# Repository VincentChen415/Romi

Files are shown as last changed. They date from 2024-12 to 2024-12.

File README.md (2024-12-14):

# Romi



Romi is a line following differential drive robot that utilizes a NUCLEO-L476RG microcontroller with addition to encoders, IMU, IR and bump sensors. The objective of the robot is to finish a black line course with a variety of patterns/obstacles similar to the one shown above.
# Romi Demo Video:
Romi Robot Demo (https://www.youtube.com/watch?v=bHqvOkEkews)

# Mechanical Design:
## Romi Chassis


The Romi chassis includes two wheels with independent drive, an encoder for each motor, and battery slot for 6 AA batteries. For our build be also opted for rechargeable lithium-ion batteries in order to limit the total cost throughout the prototyping and development process. The Romi chassis also has two rollers to prevent tipping of the robot. In addition to these aspects, the chassis also has numerous mounting points of various sizes to account for a wide range of compatible components.
## 3D-Printed Brackets


# Romi Electrical Design:
## Nucleo L476 w/ Shoe of Brian



For this Project we used a Nucleo L476 development board. This board was chosen due to the affordable and flexible nature of it. This board was also based of the STM32L476RG, which is a 32-bit ARM Cortex-M4 microcontroller with a FPU and offers very powerful processing capabilities. This board also offers a wide range of peripherals, making this a great choice for this project. This board was also paired with Shoe of Brain to provide additional outputs and additional capabilities.
## Motor Driver and Power Distribution Board for Romi Chassis


The main purpose of the motor driver and power distribution board is to step down the voltage to 5V and supply a continuous 2.5A current. The board features two DRV8838 motor drivers. The phase pin controls direction and the enable pin is a PWM input that can control the motor speed. The nSLEEP pin is acts as an enable pin on the DRV8838 motor driver. We will need 5 pins (Vcc, GND, nSLP, EN, and PH) and one timer for each motor, resulting in 10 pins and 2 timers total. 
## QTR-8RC Reflectance Sensor Array


We chose to use this sensor as a line sensor to detect when Romi starts to deviate from the physical path line. This sensor module has 8 IR LED/phototransistor pairs. Each sensor provided a separate digital I/O-measurable output in correspondence with the amount of light that is reflected to the sensor. The line, being black, reports a lesser value of reflected light. This allows us to identify where the line in relative to Romi and allows for position adjustment of robot by weighting the turning reaction the further away the line is to the center. Although this sensor module comes with 8 IR LED/phototransistors we disabled the two outmost  sensors as we found that was extra data collection that was impeding with the overall performance of the line following capabilities of Romi. 
## Right and Left Bumper Switch Assembly for Romi/TI-RSLK MAX (Through-Hole Pins Soldered)


These right and left bumper sensors contain snap-action switches with roller levers that are used to detect when Romi runs into an obstacle. For our design it was only required to program the front two snap-action switches as Romi would be approaching a flat side of an obstacle, meaning those would be the only switches to come into contact with the obstacle. These switches were forward set on the Romi in order to be the first point of contact, protecting the IR (RC) line sensor module.
## BNO055 IMU


The important outputs that the sensor can feed to the Romi are accelerations and angular rates. With this, we can take the acceleration outputs over time and integrate, resulting in velocity and position. This can also be calculated with the encoders; however, the encoder provides redundancy and any errors that the encoder will not be able to pick up. Examples of this include any wheel slip or if the motor is still able to operate but a mechanical issue may cause the robot to stop moving. The encoder will not be able to determine any angular change of the robot which the IMU provides. The IMU sensor can also pick up magnetic field strength and temperature to feed to the Romi, if needed. 
## Pin Out Diagram
PinOutDiagram

# Romi Software Design:

## State Machines
### Task 1 - Motor Controls  


The task stays in state 1 and idles the robot until the user presses the blue user input button located on the L746RG board, which would change the state to 2. In state 2, this is where the robot would follow the line and make it's way through the track. When it comes in contact with the an obstacle, the bump switches would trigger and change the Task 1 state to 3, where it performs a prescribed set of movements to manuever around the obstacle. After the prescribed set of movements, Romi would go back to the line following state to complete the course.  

The robot follows the line by utilizing the IR sensor mounted on the front of the robot for feedback to locate where the line is relative to the center of the robot. The output from the array of 8 sensors is taken, normalized and weighted (higher for the sensors further from the midpoint). This is done so that the robot corrects harder when the outer sensors read the line under it. There is a P-controller that takes the sensor output as feedback and then outputs speeds for each of the motors to stay centered on the line. The speed is fed into a PI-controller for each motor, mainly to ensure we reach and maintain our desired speeds and to provide more reliability.

### Task 2 - IMU Sensor Data


State 0 initializes all the pins and variables associated with the IMU and always moves to state 1, where it continuously reads data. 
This task was originally used as IMU sensor readings in order to provide heading feedback to the robot for precise turning and yaw control. The IMU was, at some point, set up properly and sending data. However,after a reset, we had difficulty troubleshooting the IMU as it got stuck in reset mode and we were no longer able to put it in NDOF mode. Due to this, we didn't continue with the use of an IMU and instead relied solely on the encoders and the PI controllers to do the obstacle avoidance movements. 

### Task 3 - IR Sensor Data 


State 0 initializes all the pins and variables associated with the IR sensor and always moves to state 1, where it continuously reads data. 
The IR sensor is a critical element in the system as this provides the feedback to our controller to keep the robot aligned with the black line. To read data from these sensors we have to set the pins associated with each sensor to high and then low. The amount of time it takes for the capacitor to discharge equates to a gradiant between white and black. To better this software and add more consistency, buckets for 'white', 'gray', and 'black' can be created and we can find the threshold or discharge time limits associated with each of these catagories by placing the sensor over different gradiants and taking data. Our attempt to do this was unsuccessful as the QTR-8RC on this robot was not as responsive to colors that were not purely black or white. 

The individual IR sensor data is combined into a weighed average to give line position relative to the robot.


### Task 4 - Bump Sensor Data


State 0 initializes all the pins and variables associated with the bump sensor and always moves to state 1, where it continuously reads data. 
The bump sensors were intuitive to use and easy to set up. These are simple limit switches that connect to INPUT pins with pull up resistors on the controller, which means they are active low. These bump sensors would trigger a flag that is shared with Task 1 to switch to a precribed object avoidance stage. 

## Task Diagram


This task diagram shows the period and priority for each task. The priority determines which task runs if they are both able to and period determines how long the task should take. This also shows variables that are passed between tasks. Romi primarily takes sensor data from Tasks 3 and 4 to supplement the controls that run in Task 1. Line position is sent as a float from Task 3 to Task 1 and Clear/Bump_triggered are sent between Task 1 and 3 as booleans, but in this case '1' or '0' as uint8 values. 

## Controls 


The controls for this robot consist of a P-controller for line sensor correction and a PI-controller for motor controls based on the general form a PID shown in the equation above. These controller instances are initialized from a PID class with a time delta (dt), which should match with how long the period of the task is, and an error, which is calculated from your desired value and feedback from your sensor or encoder. The line controller gains were mainly tuned with trial and error on the track. The motor controller was tuned by first bumping proportional gain until the system showed an unsteady response. The proportional gain was then lowered by 20% and increased integral gain until we achieved the response time we wanted of less than two seconds. We assumed proportional control of the line following control was enough as it didn't make sense for us to integrate any error throughout the track. The higher the proportional gain is, the more aggresively the robot will correct when it strays from the line. Shown below is the PID class and code of how to intialize the controller and the calculations needed to provide error to the controller.




From our research it was determined to be beneficial to mount the IR sensor in front of Romi to detect the required path in advance. Additionally, due to the IR sensor being mounted forward, the bump sensors also had to be mounted further forward. In order to accomplish this, multiple bracket designs were created. Our final design incorporated a IR mount with adjustable height to allow for sensor adjustments to determine the optimal position to detect the line. From testing we also decided to include a layer of electrical tape to surround the IR sensor. This was to better control the amount of ambient light that was being reflected into the sensors. This made the performance of out Romi highly repeatable.

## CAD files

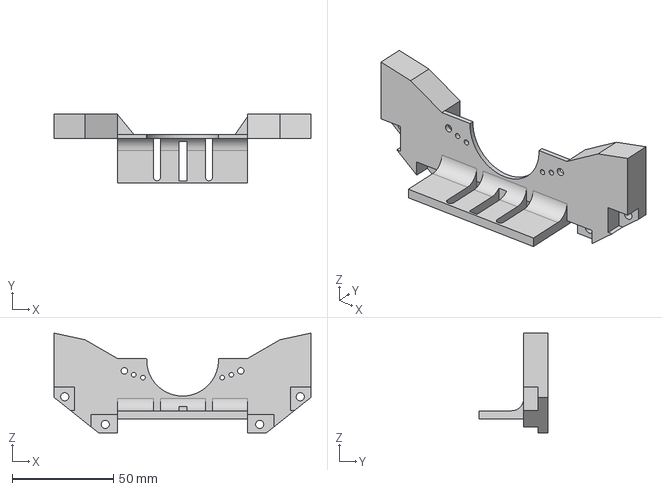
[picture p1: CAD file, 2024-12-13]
Romi CAD/IR Front Bracket.step
126.7 x 34.0 x 49.2 mm

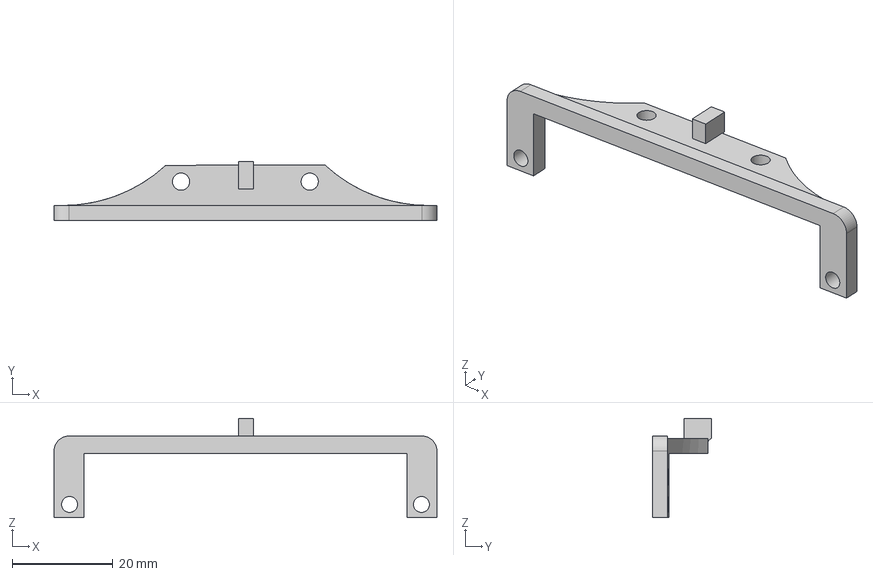
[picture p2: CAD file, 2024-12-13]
Romi CAD/IR Mount.step
76.2 x 11.7 x 19.7 mm

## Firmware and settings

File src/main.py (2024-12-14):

'''
!@file      main.py 
@brief      Drives robot around obstacle track 
@details    Uses PI-control loop, encoders, IR sensors, bump sensors, and IMU to drive robot in a circle
@author     Vincent Chen
@date       12/13/2024
'''

import micropython
from pyb import Pin, Timer, ExtInt, delay, I2C
from motor import *
from encoder import *
from sensor import * 
from PID_control import PID
import task_share
import cotask
from DiffDrive import DifferentialDriveController


# Set buffer available for troubleshooting error messages 
micropython.alloc_emergency_exception_buf(500)

# ----- Tasks -----

# Task 1 is used for motor controls 
def task1 (shares):
    state = 0 
    heading, line_position, bump_triggered, clear_share = shares
    while True:
        if state == 0:
            # Timer 2 used for motor R control
            # Timer 3 used for motor L control
            # Timer 4 used for motor L encoder 
            # Timer 8 used for motor R encoder         

            # Create a timer object to use for motor control
            tim_8 = Timer(8, freq = 20_000)
            tim_4 = Timer(4, freq = 20_000)

            # Create an L6206 motor object 
            mot_L = Motor(tim_4, CH = 1, PWM_pin = Pin.cpu.B6, PH_pin = Pin.cpu.C7, EN_pin = Pin.cpu.A9)
            mot_R = Motor(tim_8, CH = 1, PWM_pin = Pin.cpu.C6, PH_pin = Pin.cpu.C8, EN_pin = Pin.cpu.C9)


            # Create a timer object to use for encoder monitoring
            tim_3 = Timer(3, period = 65_535, prescaler = 0)
            tim_2 = Timer(2, period = 65_535, prescaler = 0)

            # Create an L6206 motor encoder object
            enc_L = Encoder(tim_3, CH_A = 1, CH_B = 2, CH_A_pin = Pin.cpu.B4, CH_B_pin = Pin.cpu.B5)
            enc_R = Encoder(tim_2, CH_A = 1, CH_B = 2, CH_A_pin = Pin.cpu.A0, CH_B_pin = Pin.cpu.A1)
            
            # Enable the L6206 driver
            mot_L.enable()
            mot_R.enable()
            

            # Creat PID controller for line following
            pid_line = PID(kp=0.31, ki=0.0, kd=0.0)  # Adjust gains as needed

            # Romi parameter data
            track_width = 0.141 # meters 
            desired_vel = 0.31 # m/s
            max_pwm = 30 
            start_heading = heading.get()
            #print("Start Heading: ", start_heading)

            # Initialize PID objects for motors
            pid_left = PID(kp=87, ki=75, kd=0.00)
            pid_right = PID(kp=87, ki=75, kd=0.00)

            # Initialize object for manually driving 
            diff_drive = DifferentialDriveController (
                            motor_left = mot_L,
                            motor_right = mot_R,
                            encoder_left = enc_L,
                            encoder_right = enc_R, 
                            counts_per_meter = 2329, 
                            track_width = 0.141,
                            control_left =  pid_left,
                            control_right = pid_right)

            # Clear = 1 when drive finishes            
            clear = 0
            clear_share.put(clear)
            state = 1
        
        elif state == 1:
            # Blue user button is used as a start condition for the romi
            global button_pressed
            mot_L.set_duty(0)
            mot_R.set_duty(0)
            if button_pressed == True:
                state = 2
            else:
                state = 1


        elif state == 2:
            # Check to see if the drive sequence in state 3 has finished. If so, set flag 
            bump = bump_triggered.get()
            if bump == 1 and clear == 0:
                mot_L.set_duty(0)
                mot_R.set_duty(0)
                state = 3
            else:
                state = 2

            # Delta time between each controller update, should match the period of the task 
            dt = 0.01

            # Get currrent line position 
            line_value = line_position.get()

            # Value indicating weighed average is center 
            desired_position = 0  
            
            # Desired position - actual position
            line_error = desired_position - line_value

            # Factor to add/subtract from motor speeds to account for error
            steering_adjust = pid_line.update(line_error, dt)

            # Get ideal moving speeds
            left_speed = desired_vel - steering_adjust
            right_speed = desired_vel + steering_adjust

            #print('Line Error: ', line_error)
            #print('Steering adjust: ', steering_adjust)
            
            # Update Encoders to get encoder encoder readings 
            enc_R.update()
            enc_L.update()

            # Get actual left and right velocities
            actual_left = enc_L.get_velocity()
            actual_right = enc_R.get_velocity()

            # Get error in desired and actual speed for each wheel
            error_left = left_speed - actual_left
            error_right = right_speed - actual_right

            #print("desired left: ", left_speed)
            #print("Actual left: ", actual_left)
            #print("desired right: ", right_speed)
            #print("Actual right: ", actual_right)
            # Put into PID controller to get output PWM
            left_pwm = pid_left.update(error_left,dt)
            right_pwm = pid_right.update(error_right,dt)
            
            # Set motor PWM Limits
            left_pwm = max(0, min(left_pwm, max_pwm))
            right_pwm = max(0, min(right_pwm, max_pwm))

            #print('Left pwm: ' , left_pwm)
            #print('Right pwm: ' , right_pwm)
           
            mot_L.set_duty(left_pwm)
            mot_R.set_duty(right_pwm)
            #If an obstacle is detected, transition to obstacle avoidance
 
        
        elif state == 3:
            # This is a predesignated drive sequence that allows the Romi to move around obstacle when bump sensors are activated
            #print('State 3 reached')
            mot_L.set_duty(0)
            mot_R.set_duty(0)
            delay(250)
            diff_drive.drive_distance(distance= -0.5, speed = 0.25)
            delay(250)
            diff_drive.turn_angle(150, 0.2)
            delay(250)
            diff_drive.drive_distance(distance= 1.5, speed = 0.25)
            print("finished going forward")
            delay(250)
            diff_drive.turn_angle(-270, 0.2)
            print("Finished turning")
            delay(250)
            diff_drive.drive_distance(distance = 1.25, speed = 0.25)
            print('Finished driving')
            # When the drive sequence has finished, set clear flag to true
            clear = 1
            clear_share.put(clear)
            print("Clear value : ", clear)

            state = 2

        # State 4 is to alternative to drive around the box (UNUSED)
        elif state == 4:
            heading_tolerance = 0.5
            drive_radius = 0.305 # m 
            # one_rev = 2 * 3.1314 * (drive_radius + track_width/2) 
            angular_velocity = desired_vel / drive_radius

            dt = 0.05  # Example time step (this should match your scheduler period or calculated dt)
            position_R = enc_R.get_position() * 2 * 3.1415 * 0.070 / 1024
            # print('Current Position: ', position_R)
            # print('Desired position: ', one_rev)

            enc_R.update()
            enc_L.update()

            # Update sensor readings and set motor parameters 
            left_velocity = desired_vel - (angular_velocity * track_width / 2)
            right_velocity = desired_vel + (angular_velocity * track_width / 2)
            print('Desired left velocity ', left_velocity)
            print('Desired right velocity ', right_velocity)
            # Read encoder data
            
            actual_left = enc_L.get_velocity()
            actual_right = enc_R.get_velocity()
            print("Actual left :" + str(actual_left))
            print("Actual right :" + str(actual_right))
            

            # Errors 
            error_left = left_velocity - actual_left
            error_right = right_velocity - actual_right

            #print("Error_left: " + str(error_left))
            #print("Error_right: " + str(error_right))
            
            left_out = pid_left.update(error_left, dt)
            right_out = pid_right.update(error_right, dt)

            print("Error Left: " + str(left_out))
            print("Error Right: " + str(right_out))
            print('\n')

            left_duty_cycle = (left_out / left_velocity) * 100
            right_duty_cycle = (right_out / right_velocity) * 100
            

            #print("Left Duty cycle: ", left_duty_cycle)
            #print("Right Duty cycle: ", right_duty_cycle)

            mot_L.set_duty(left_duty_cycle)
            mot_R.set_duty(right_duty_cycle)
            
            heading_current = heading.get()
            print('Current Heading: ' + str(heading_current))

            # End condition is when the header of the robot is the same as start
            if abs(heading_current - start_heading) < heading_tolerance and position_R > 100:
                print("Circle completed. Stopping motors.")
                button_pressed = False
                state = 1  # Transition to stop state or another appropriate state

            #else:
            state = 2

        yield (state)
 

# IMU data collection 
def task2 (shares):
    state = 0
    heading, line_position = shares

    while True:
        if state == 0:
            i2c3 = I2C(3, I2C.MASTER, baudrate=400_000)                 # Initialize I2C Bus 1; pins are PB8 for SCL and PB9 for SDA    
            imu = BNO055(i2c3, reset_pin=Pin.cpu.C5)                    # Create an IMU object
            delay(400)                                                  # Delay to let IMU initiate
            imu.mode = 'NDOF'                                           # Set sensor to NDOF mode
            state = 1                                                   # Move to next state after calibration

        elif state == 1:
            #current_heading = imu.eul_angles()[0]/16
            #print('Current_heading', current_heading)
            
            # Troubleshooting IMU
            OPR_MODE_REG = 0x3D                                         # Register address for OPR_MODE
            current_mode = i2c3.mem_read(1, 0x28, OPR_MODE_REG)         # Read the operating mode from the IMU
            print(f"Current Operating Mode: {current_mode[0]:#02x}")    # Print the mode value

            sys_status = i2c3.mem_read(1, 0x28, 0x00)                   # Read 1 byte from SYS_STATUS register
            print(sys_status)                                           # Print the SYS_STATUS

            # You can map the value to specific modes:
            if current_mode[0] == 0x00:
                print("IMU is in CONFIG mode")
            elif current_mode[0] == 0x01:
                print("IMU is in ACCELEROMETER mode")
            elif current_mode[0] == 0x02:
                print("IMU is in MAGNETOMETER mode")
            elif current_mode[0] == 0x03:
                print("IMU is in GYROSCOPE mode")
            elif current_mode[0] == 0x0C:
                print("IMU is in NDOF mode")

            # heading.put (current_heading)                             # Get heading reading and put into share for task 1
            # ang_vel_x, ang_vel_y, ang_vel_z = imu.ang_vel()            # Read Angular Velocity (x, y, z)
            # print(f"Angular Velocity - X: {ang_vel_x / 16.0:.2f}°/s, Y: {ang_vel_y / 16.0:.2f}°/s, Z: {ang_vel_z / 16.0:.2f}°/s")

            state = 1
        yield (state)

# IR sensor data task 
def task3 (shares):
    state = 0
    heading, line_value = shares
    while True:
        if state == 0:
            
            # Initialize sensor pins for reading IR sensor outputs            
            qtr = QTR8RC(sensor_pins = ['A8', 'B10', 'B12', 'B11', 'B2', 'B1', 'B15', 'B14'], 
                         led_pin= Pin.cpu.B13, 
                         timeout_us=5000)
            
            # Turn the LEDs on so sensors can take readings 
            qtr.turn_leds_on()

            state = 1        

        elif state == 1:
            # Read reflectance values of each sensor in array and print 
            reflectance_values = qtr.read()
            #print("Reflectance values:", reflectance_values)
            
            # Print line position relative to robot, 0 is centered, - means line is on left, + means line is on right
            line_position = qtr.read_line_position()
            #print("Line Position: ", line_position)

            # Put the line_value into shares for task 1 to use
            line_value.put (line_position)

            state = 1
        yield (state)


# Bump sensor task 
def task4 (shares):
    state = 0
    bump_triggered,clear_share = shares
    while True:
        if state == 0:

            # Pins for the left bump sensor
            left_pins = {'BMP3': Pin.cpu.A10 , 'BMP4': Pin.cpu.B3, 'BMP5': Pin.cpu.C4}

            #Pins for the right bump sensor
            right_pins = {'BMP0': Pin.cpu.A4 , 'BMP1': Pin.cpu.H0, 'BMP2': Pin.cpu.H1}
            
            # Initialize bump sensor instance for left and right
            left_bumper = BumpSensor(left_pins)
            right_bumper = BumpSensor(right_pins)

            # Bump sense flag = 0 when no collision, 1 when collided with obstacle 
            bump_sense = 0

            state = 1

        elif state == 1:
            #print('REACHED TASK 4')
            
            clear = clear_share.get()
            #print("Clear value : ", clear)
            #print("Bump value : ", bump_sense)

            if clear == 1:
                bump_sense = 0
            left_states = left_bumper.read()
            right_states = right_bumper.read()

            if left_bumper.pressed('BMP3') or right_bumper.pressed('BMP2'):
                print("Bumpers pressed:", left_states, right_states)
                bump_sense = 1

            bump_triggered.put(bump_sense)
                
            state = 1

        yield (state)

# Callback function to wait for button press, looking back - didn't need to be an interrupt
def tim_cb (cb_src):
    global button_pressed
    button_pressed = True

if __name__ == '__main__':
    button_pressed = False

    # Button initialzie to start the Romi code
    button_int = ExtInt(Pin.cpu.C13, ExtInt.IRQ_FALLING,Pin.PULL_DOWN, tim_cb)

    # Variables that are used in between tasks
    # 'f' is float type
    # 'H' is unsigned short type

    heading = task_share.Share ('f', 100, name= "Heading")
    line_position = task_share.Share('f', 100, name = "line_position")
    bump_triggered = task_share.Share ('H', 100, name="bump_triggered")
    clear_share = task_share.Share('H', 100, name = "clear_share" )

    # Initialize tasks in the FSM 
    task1 = cotask.Task (task1, name = 'Task 1', priority = 4, 
                        period = 10, profile = True, trace = True, shares = (heading, line_position, bump_triggered, clear_share))
    task2 = cotask.Task (task2, name = 'Task 2', priority = 3, 
                        period = 50, profile = True, trace = True, shares = (heading, line_position))
    task3 = cotask.Task (task3, name = 'Task 3', priority = 2, 
                        period = 10, profile = True, trace = True, shares = (heading, line_position))
    task4 = cotask.Task (task4, name = 'Task 4', priority = 1, 
                        period = 5, profile = True, trace = True, shares = (bump_triggered, clear_share))
    
    # Add the task to the list (so it will be run) and run scheduler
    cotask.task_list.append (task1)
    #cotask.task_list.append (task2)        # Disabled because IMU was not working 
    cotask.task_list.append (task3)
    cotask.task_list.append (task4)

    while True: 
        cotask.task_list.pri_sched ()

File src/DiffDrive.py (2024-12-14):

'''
!@file          DiffDrive.py
@brief          A driver for a controller that will control manual movement of the robot 
@details        Two function include turning and driving a prescribed angle/distance. 
                This is used for obstacle avoidance when bump sensors are triggered
@author         Vincent Chen
@date           December 13th, 2024
'''


from pyb import Timer, Pin, delay
import time

class DifferentialDriveController:
    def __init__(self, motor_left, motor_right, encoder_left, encoder_right, counts_per_meter, track_width, control_left=None, control_right=None):
        """
        !@brief Initialize the differential drive controller.
        @details Diff Drive controller is used for 
        @param motor_left: Motor object for the left motor.
        @param motor_right: Motor object for the right motor.
        @param encoder_left: Encoder object for the left motor.
        @param encoder_right: Encoder object for the right motor.
        @param counts_per_meter: Encoder counts per meter of travel.
        @param track_width: Distance between the two wheels (in meters).
        @param pid_left: PID object for the left motor.
        @param pid_right: PID object for the right motor.
        """
        self.motor_left = motor_left
        self.motor_right = motor_right
        self.encoder_left = encoder_left
        self.encoder_right = encoder_right
        self.counts_per_meter = counts_per_meter
        self.track_width = track_width
        self.pid_left = control_left
        self.pid_right = control_right

    def reset_encoders(self):
        '''
        !@brief Resets encoders
        @details Reset both encoders to zero
        '''
        self.encoder_left.zero()
        self.encoder_right.zero()

    def drive_distance(self, distance, speed):
        """
        !@brief Drive a specified distance (in meters) at a given speed using PID to prevent drift.
        @details Takes in a distance and a speed to drive the robot with the use of a PI controller 
        @param distance: Distance to drive (positive for forward, negative for reverse).
        @param speed: Speed to drive the motors (as a percentage, 0-100).
        """

        
        target_counts = distance * self.counts_per_meter    # Distance need to travel in counts
        self.reset_encoders()                               # Resets the encoder position

        # Initialize PID controllers if provided
        if self.pid_left: self.pid_left.reset()              
        if self.pid_right: self.pid_right.reset()

        # Set motor direction based on the sign of the distance
        if distance > 0:
            speed = speed
        else:
            speed = -speed

        while True:
            # Update encoders to get current readings
            self.encoder_left.update()
            self.encoder_right.update()

            # Get current position travelled
            left_counts = self.encoder_left.get_position()
            right_counts = self.encoder_right.get_position()

            # Get current velocities 
            actual_left = self.encoder_left.get_velocity()
            actual_right = self.encoder_right.get_velocity()
            
            # Desired velocity is from the input 
            left_velocity = speed
            right_velocity = speed

            # Calculate error between the left and right encoder counts
            error_left = left_velocity - actual_left
            error_right = right_velocity - actual_right

            # Update period of 100ms
            dt = 0.1              

            # Ramp speed with PI controller 
            if self.pid_left:
                pid_output_left = self.pid_left.update(error_left, dt)
                #print("PWN :", speed + pid_output_left)
                self.motor_left.set_duty(speed + pid_output_left)
            if self.pid_right:
                pid_output_right = self.pid_right.update(error_right, dt)
                self.motor_right.set_duty(speed + pid_output_right)
                #print("PWM: ", speed+pid_output_right)

            # Stop when the target distance is reached
            if abs(left_counts) >= abs(target_counts) and abs(right_counts) >= abs(target_counts):
                break
        
        # After distance reached, stop motors 
        self.motor_left.set_duty(0)
        self.motor_right.set_duty(0)

    def turn_angle(self, angle, speed):
        """
        !@brief Turn in place by a specified angle (in degrees) using PID to prevent drift.
        @details Uses PID controller to precisely turn Romi in place  
        @param angle: Angle to turn (positive for clockwise, negative for counter-clockwise).
        @param speed: Speed to drive the motors during the turn (as a percentage, 0-100).
        """
        # Calculate the distance the wheels need to move to achieve the desired angle
        wheel_circumference = self.track_width * 3.14159                    # Get circumference of wheel
        turn_distance = (angle / 360) * wheel_circumference                 # How far you have to travel based on arc length
        target_counts = turn_distance * self.counts_per_meter               # The counts from encoder to reach specified arc length

        self.reset_encoders()                                               # Clean current encoder data

        # Initialize PID controllers if provided
        if self.pid_left: self.pid_left.reset()
        if self.pid_right: self.pid_right.reset()

        # Set initial motor duty cycles for turning
        if angle > 0:                                                       # Clockwise turn (positive angle)
            left_speed = speed
            right_speed = -speed
        else:                                                               # Counter-clockwise turn (negative angle)
            right_speed = speed
            left_speed = -speed

        while True:
            # Update encoder positions
            self.encoder_left.update()
            self.encoder_right.update()

            # Get current encoder position
            left_counts = self.encoder_left.get_position()
            right_counts = self.encoder_right.get_position()

            # Get the current velocities
            actual_left = self.encoder_left.get_velocity()
            actual_right = self.encoder_right.get_velocity()

            # Calculate the error between the actual velocities and the target velocities
            error_left = left_speed - actual_left
            error_right = right_speed - actual_right


            dt = 0.1                                                        # Delta t used in control loop/update speed

            # Ramp speed with PI controller 
            if self.pid_left:
                pid_output_left = self.pid_left.update(error_left, dt)
                self.motor_left.set_duty(speed + pid_output_left)
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

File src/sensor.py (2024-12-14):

'''
!@file      sensor.py
@brief      A driver for reading from IMU, IR, and Bump sensors used in Romi
@details    Used to read encoder, IR sensor, and bump sensor data to assist robot in manuevering course
@author     Vincent Chen
@date       December 13, 2024
'''

from pyb import Pin, I2C, delay, micros
import struct

class BNO055:
    '''
    @brief A driver for setting up and reading from IMU
    @details Functions include intializing the IMU, picking the mode, calibration, and reading data
    '''
    def __init__(self, i2c, reset_pin, address = 0x28):
        '''
        !@brief Init function for setting up BNO055 IMU
        @details Set up IMU with i2c bus, reset pin and address (0x28 is default)
        @param reset_pin Pin associated with reset signal
        @param address 0x28 is device address for this IMU
        '''
        self.i2c = i2c
        self.address = address
        self.RST = Pin(reset_pin, Pin.OUT_PP)

    def cal_status(self):
        '''
        !@brief Determine calibration statuses for gyroscope, accelerometer, and magnetometer
        @details Read from addresses to determine statuses of each sensor
        '''
        status = self.i2c.mem_read(1, self.address, 0x35)
        sys_status, gyro_status, accel_status, mag_status = (status[0] >> 6 & 0x03, 
                                                             status[0] >> 4 & 0x03, 
                                                             status[0] >> 2 & 0x03, 
                                                             status[0] & 0x03)
        return sys_status, gyro_status, accel_status, mag_status


    def mode(self, mode_name):
        '''
        !@brief Function to change the IMU mode to IMU, Calibrating, etc.
        @details Writes to IMU register for mode change (0x3D)
        @param mode_name, mode which is associated with a hex number we can write to register for sensor mode
        '''
        modes = {
            "IMU": 0x08,
            "COMPASS": 0x09,
            "M4G": 0x0A,
            "NDOF_OFF": 0x0B,
            "NDOF": 0x0C,
        }
        if mode_name.upper() in modes:
            self.i2c.mem_write(modes[mode_name.upper()], self.address, 0x3D)
            delay(650)
            set_mode = self.i2c.mem_read(1, self.address, 0x3D)[0]
            if set_mode != modes[mode_name.upper()]:
                raise ValueError(f"Failed to set mode to {mode_name}")
        else:
            raise ValueError("Invalid mode selected.")

    def cal_coeff(self):
        '''
        !@brief Reads calibration coefficients
        @details Reads 22 bytes from register 0x55 to determine calibration coefficients
        '''

        # I2C.mem_read(data, addr, memaddr, *, timeout=5000, addr_size=8)
        # data can be an integer (number of bytes to read) or a buffer to read into
        # addr is the I2C device address
        # memaddr is the memory location within the I2C device
        # timeout is the timeout in milliseconds to wait for the read
        # addr_size selects width of memaddr: 8 or 16 bits

        return self.i2c.mem_read(22, self.address, 0x55)  # read 22 bytes 

   
    def calibrate(self):
        '''
        @brief Perform the full calibration process
        @details This includes the figure-eight dance for the magnetometer, six-step for the accelerometer, 
                 and holding still for the gyroscope.
        '''
        # Step 1: Set to NDOF mode for full sensor fusion
        self.mode = 'NDOF'

        print("Magnetometer: Perform the figure-eight calibration dance.")
        while True:
            sys, gyro, accel, mag = self.cal_status()
            if mag == 3:
                break  # Magnetometer is calibrated
            print(f"Mag Calib Status: {100 / 3 * mag:3.0f}%")
            delay(1)
        print("... CALIBRATED")
        delay(1)

        print("Accelerometer: Perform the six-step calibration dance.")
        while True:
            sys, gyro, accel, mag = self.cal_status()
            if accel == 3:
                break  # Accelerometer is calibrated
            print(f"Accel Calib Status: {100 / 3 * accel:3.0f}%")
            delay(1)
        print("... CALIBRATED")
        delay(1)

        print("Gyroscope: Perform the hold-in-place calibration dance.")
        while True:
            sys, gyro, accel, mag = self.cal_status()
            if gyro == 3:
                break  # Gyroscope is calibrated
            print(f"Gyro Calib Status: {100 / 3 * gyro:3.0f}%")
            delay(1)
        print("... CALIBRATED")
        delay(1)

        print("\nCALIBRATION COMPLETED")

        # Retrieve and print calibration offsets
        print("Insert these preset offset values into project code:")
        offsets = self.read_calibration_data()
        print(f"  Offsets_Magnetometer:  {offsets['magnetometer']}")
        print(f"  Offsets_Gyroscope:     {offsets['gyroscope']}")
        print(f"  Offsets_Accelerometer: {offsets['accelerometer']}")

    def read_calibration_data(self):
        '''
        @brief Read calibration data from the IMU's memory.
        @details Read and return the calibration data for the magnetometer, gyroscope, and accelerometer.
        Some help/reference: https://learn.adafruit.com/adafruit-bno055-absolute-orientation-sensor/bno055-sensor-calibration-circuitpython
        '''
        # Memory addresses for calibration data (These are standard for BNO055)
        mag_offset_addr = 0x55
        gyro_offset_addr = 0x61
        accel_offset_addr = 0x55

        # Reading calibration data (6 bytes each for magnetometer, gyroscope, accelerometer)
        magnetometer = self.i2c.mem_read(6, self.address, mag_offset_addr)
        gyroscope = self.i2c.mem_read(6, self.address, gyro_offset_addr)
        accelerometer = self.i2c.mem_read(6, self.address, accel_offset_addr)

        # Unpack the calibration data
        mag_offsets = struct.unpack('<hhh', bytes(magnetometer))
        gyro_offsets = struct.unpack('<hhh', bytes(gyroscope))
        accel_offsets = struct.unpack('<hhh', bytes(accelerometer))

        # Return a dictionary with the offsets
        return {
            "magnetometer": mag_offsets,
            "gyroscope": gyro_offsets,
            "accelerometer": accel_offsets
        }


    def eul_angles(self):
        '''
        !@brief Reads euler angles from IMU
        @details Reads 6 bytes from register 0x1A to determine heading, roll, and pitch
        @return Heading, pitch, and roll based on movement of robot (Only heading was used in this case)
        '''
        data = self.i2c.mem_read(6, self.address, 0x1A)
        heading, roll, pitch = struct.unpack('<hhh', data)
        return heading, roll, pitch
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
